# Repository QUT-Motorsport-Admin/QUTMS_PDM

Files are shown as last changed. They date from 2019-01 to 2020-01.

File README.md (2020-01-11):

QUTMS Banner

# Power Distribution Module

Main power distribution for high current devices on the car as well as control of the main LV power busses.

## Features

- ATmega1280 microcontroller
- 4 high and low side outputs
- 9 high current high-side outputs
- 2 Analog inputs
- Onboard thermistor temperature sensor
- CANBUS communication with the MCP2515 controller

## Functions

A key function of the PDM is to power the shutdown loop that runs throughout the car powering the AIRs. This uses one of the high current outputs and the low side of one of the high-low outputs.

The PDM controls power to all of the low voltage devices on the car through a few of its high current outputs. While the current limit on each high current output is 7.5 amps, devices are split onto multiple outputs to allow for future expansion.

Every output on the PDM is controlled using pins on the microcontroller that have PWM capability. This is so devices like pumps and fans can have their speeds modulated. 

The two analog inputs are intended to be used for the radiator temperature sensors since the PDM is also controlling the radiator fans.

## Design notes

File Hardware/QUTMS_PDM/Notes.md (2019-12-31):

# PDM Notes

Outputs with sense wires on the PCB schematic:
- HIC8
- HIC9
- HL3
- HL4

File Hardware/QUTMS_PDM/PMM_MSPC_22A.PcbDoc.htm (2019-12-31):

Reporting Options

# File in Previous Format

Date | : | 19/12/2019
Time | : | 10:54:37 AM
Filename | : | C:\Users\leo2a\Documents\GitHub\QUTMS_PDM\Hardware\QUTMS_PDM\PMM_MSPC_22A.PcbDoc

Version | Warning
Summer 09 | CAUTION - File contains old violation objects. These violations are no longer supported & will not be loaded. Please run DRC after opening this file in order to refresh the violations.
Summer 09 | CAUTION - Existing testpoint rules and settings are used as fabrication testpoint information.
Release 12 | CAUTION - Air Gap Width previously controlled by Clearance rule is now controlled by Polygon Connect Style rule's newly introduced Air Gap Width (set to default value). Suggest reviewing each Polygon Connect Style rule's Air Gap Width attribute for correctness.
Release 13 | CAUTION - Silkscreen Over Component Pads Rules are converted to Silk To Solder Mask Clearance Rules. Suggest examining rule scopes for accuracy.

This file was generated by an earlier version of the software

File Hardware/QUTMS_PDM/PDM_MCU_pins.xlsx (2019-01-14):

Pin | PORT | Function
1 | PORTG 5 | PWM12 | HL3
2 | PORTE 0 | LEDamber
3 | PORTE 1 | LEDgreen
4 | PORTE 2
5 | PORTE 3 | PWM9 | HC9
6 | PORTE 4 | PWM1 | HC3
7 | PORTE 5 | PWM2 | HC2
8 | PORTE 6
9 | PORTE 7
10 | VCC | 5V
11 | GND | GND
12 | PORTH 0
13 | PORTH 1
14 | PORTH 2
15 | PORTH 3 | PWM7 | HC7
16 | PORTH 4 | PWM3 | HC1
17 | PORTH 5 | PWM4 | HC4
18 | PORTH 6 | PWM11 | HL2
19 | PORTB 0 | SS
20 | PORTB 1 | SCK
21 | PORTB 2 | MOSI
22 | PORTB 3 | MISO
23 | PORTB 4 | PWM10 | HL1
24 | PORTB 5
25 | PORTB 6
26 | PORTB 7 | PWM13 | HL4
27 | PORTH 7
28 | PORTG 3
29 | PORTG 4
30 | RESET | RST
31 | VCC | 5V
32 | GND | GND
33 | XTAL2 | XT
34 | XTAL1 | XT
35 | PORTL 0
36 | PORTL 1 | PWM5 | HC5
37 | PORTL 2 | PWM8 | HC8
38 | PORTL 3 | PWM6 | HC6
39 | PORTL 4
40 | PORTL 5
41 | PORTL 6
42 | PORTL 7
43 | PORTD 0
44 | PORTD 1
45 | PORTD 2
46 | PORTD 3
47 | PORTD 4
48 | PORTD 5
49 | PORTD 6
50 | PORTD 7
51 | PORTG 0 | HL34_DISABLE
52 | PORTG 1 | HL34_ENABLE
53 | PORTC 0
54 | PORTC 1
55 | PORTC 2
56 | PORTC 3
57 | PORTC 4
58 | PORTC 5
59 | PORTC 6
60 | PORTC 7
61 | VCC | 5V
62 | GND | GND
63 | PORTJ 0
64 | PORTJ 1 | HL34_status
65 | PORTJ 2 | HL12_status
66 | PORTJ 3 | HL12_enable
67 | PORTJ 4 | HL12_disable
68 | PORTJ 5 | CAN_RX0_buf
69 | PORTJ 6 | CAN_INT
70 | PORTG 2 | HIC9_ser
71 | PORTA 7 | HL4_ser
72 | PORTA 6 | HIC8_ser
73 | PORTA 5 | HL3_ser
74 | PORTA 4 | AN2_bias
75 | PORTA 3 | AN1_bias
76 | PORTA 2 | CAN_TX0_RTS
77 | PORTA 1 | CAN_RST
78 | PORTA 0 | CAN_select
79 | PORTJ 7
80 | VCC | 5V
81 | GND | GND
82 | PORTK 7 | Vbatt
83 | PORTK 6 | 5V
84 | PORTK 5 | AN2
85 | PORTK 4 | AN1
86 | PORTK 3 | Thermistor
87 | PORTK 2 | HC5_current
88 | PORTK 1 | HC4_current
89 | PORTK 0 | HC3_current
90 | PORTF 7 | HC2_current
91 | PORTF 6 | HL34_current
92 | PORTF 5 | HL12_current
93 | PORTF 4 | HC9_current
94 | PORTF 3 | HC8_current
95 | PORTF 2 | HC6_current
96 | PORTF 1 | HC7_current
97 | PORTF 0 | HC1_current
98 | AREF | AREF
99 | GND | GND
100 | AVCC | AVCC

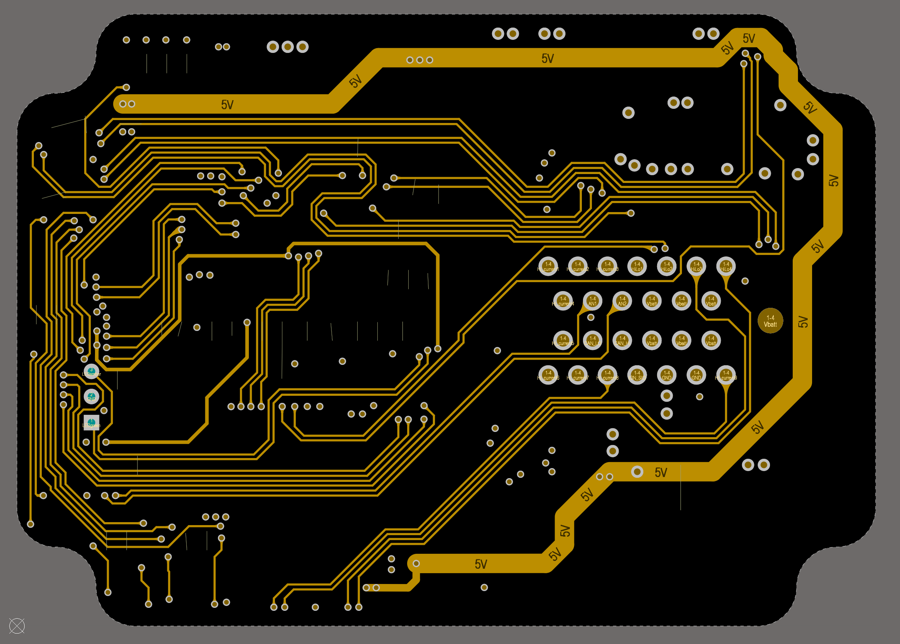
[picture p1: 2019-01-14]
Hardware/QUTMS_PDM/PDMMid.PNG

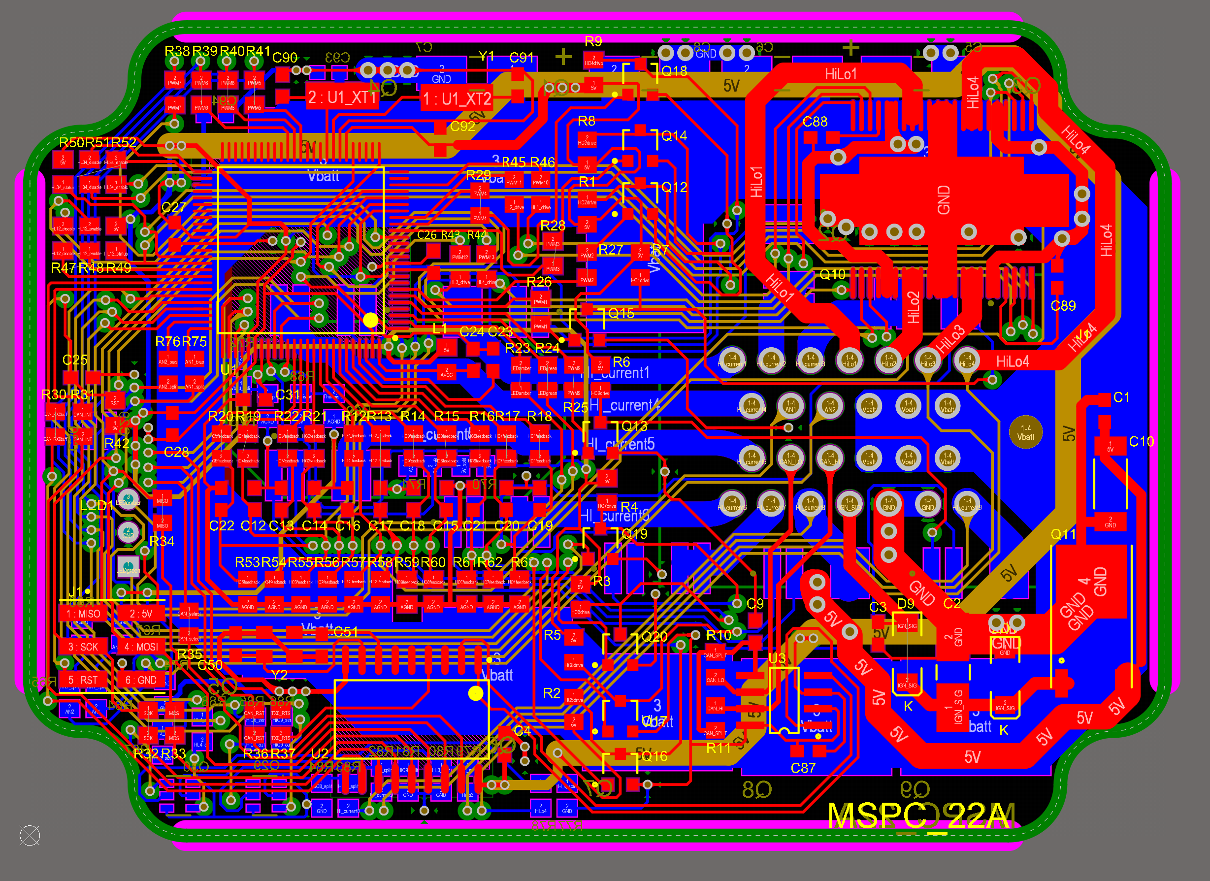
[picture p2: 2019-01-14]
Hardware/QUTMS_PDM/PDMAll.PNG

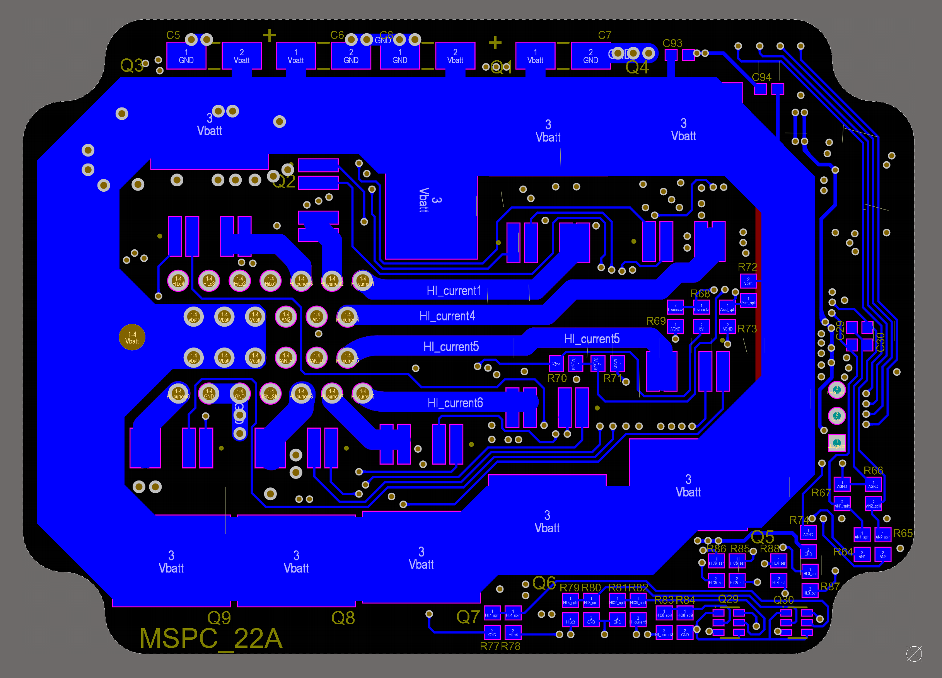
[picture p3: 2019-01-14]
Hardware/QUTMS_PDM/PDMBtmFlipped.PNG

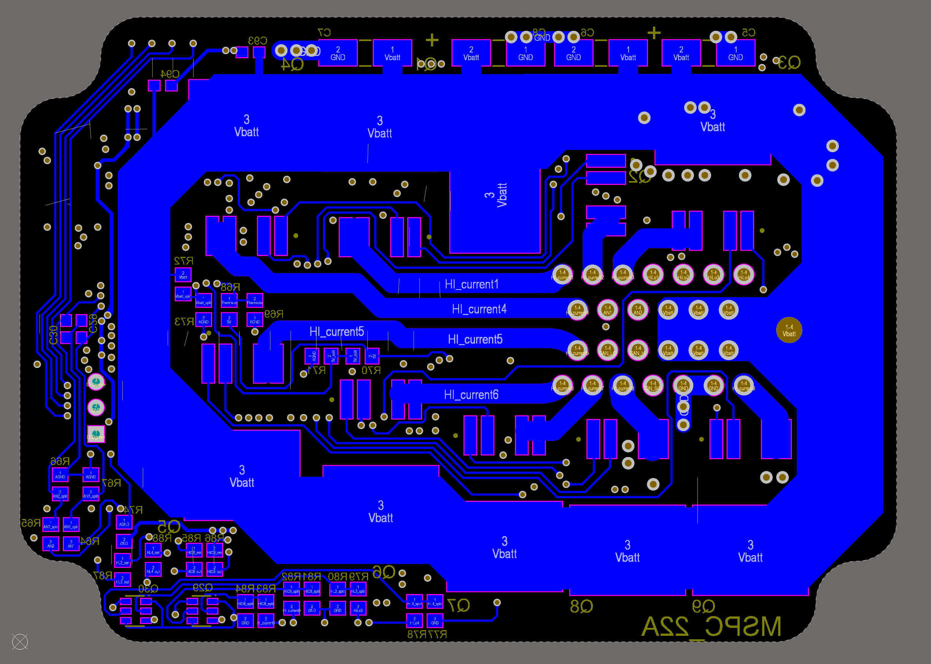
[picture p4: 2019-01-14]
Hardware/QUTMS_PDM/PDMBtm.PNG

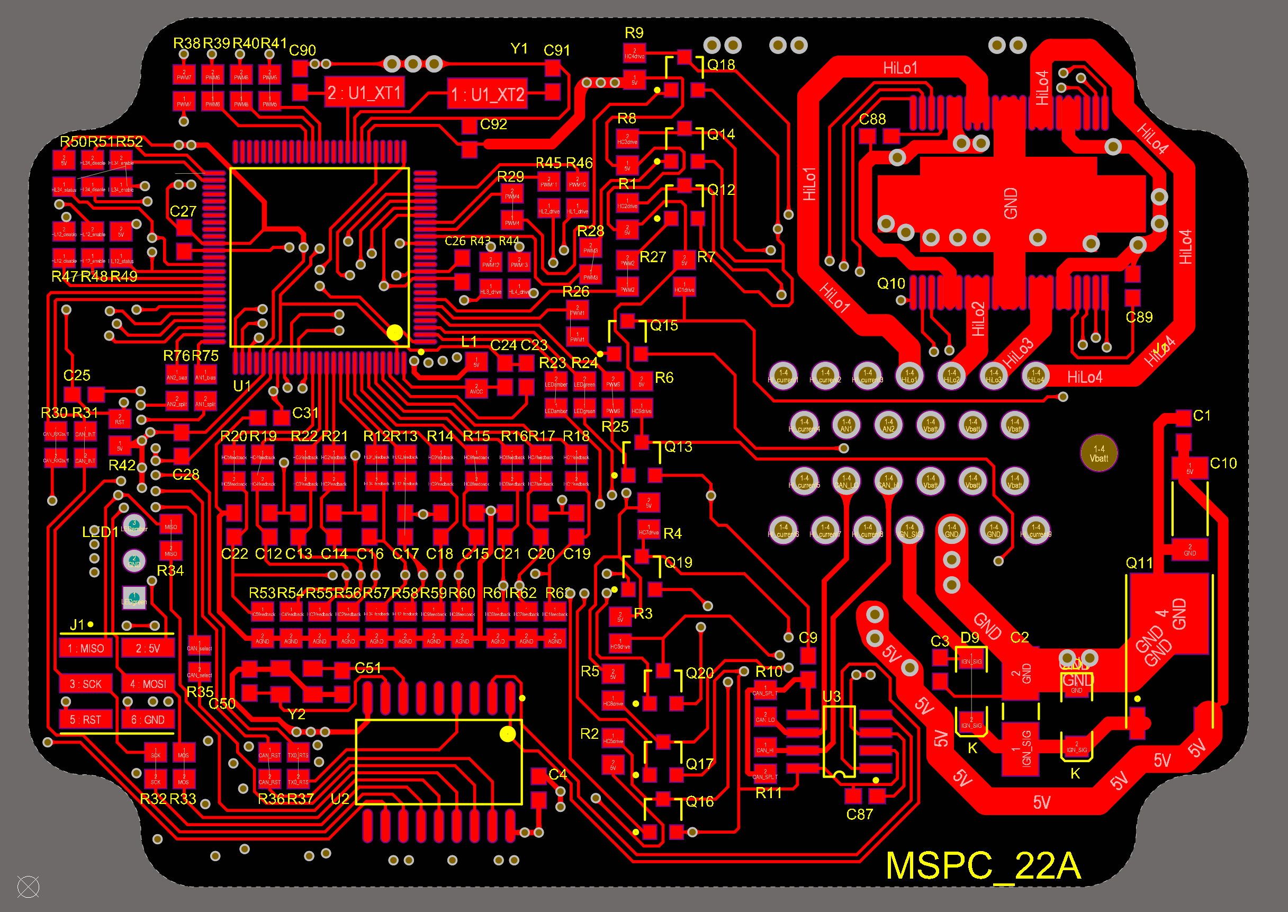
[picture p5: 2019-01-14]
Hardware/QUTMS_PDM/PDMTop.PNG

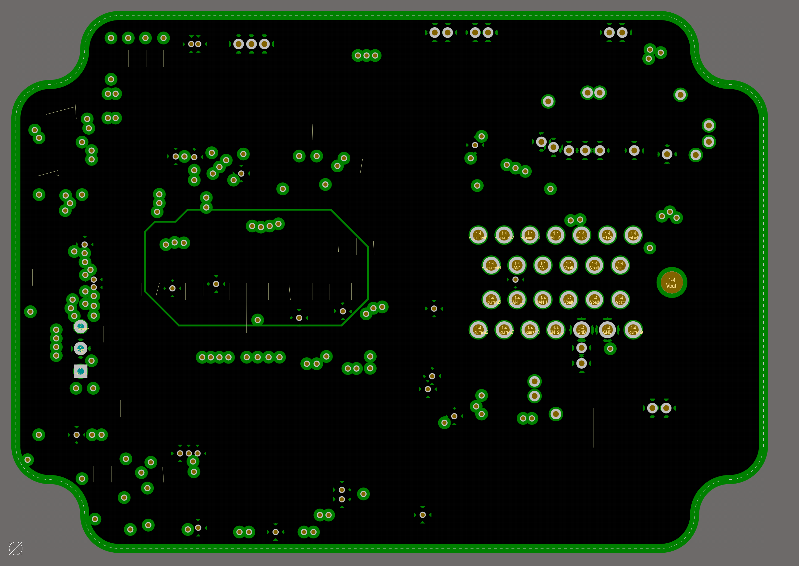
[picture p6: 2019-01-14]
Hardware/QUTMS_PDM/PDMGnd.PNG

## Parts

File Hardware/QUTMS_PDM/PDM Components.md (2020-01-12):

PDM Components

ID		NAME		QTY		DESC
---		---			---		---
C1		?			1		106 50K (144/Q51)
C2-8	2521 Cap	1		106 50K (144/Q51)
C10		2521 Cap	1		106 50K (144/Q51)
C90		0603 Cap	1		22pf 16V Ceramic
C91		0603 Cap	1		22pf 16V Ceramic
Y1		A16012X		1		16Mhz Crystal
U1		ATMEGA1280	1		Microcontroller
U2		MCP2515		1		CAN Controller
U3		
Q1-Q9	AUIR3320S	9		Alternative: AUIR3313STRL
Q10 	MC33932VW	1
Q12-Q20	1702A		9
Q29-Q30 X17			2		
J1		2x3 Header	1		ICSP Programming Header
L1		0805		1		Inductor
R1-11	0603 ?Ω		10		Unpopulated Resistor
R12-22	0603 10kΩ	10		Resistor
R30-37	0603 0Ω		8		Resistor
R38-41	0603 1kΩ	4		Resistor

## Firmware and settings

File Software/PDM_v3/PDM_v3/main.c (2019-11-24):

/*
 * PDM_v3.c
 *
 * Updated : 6/03/2019 4:09:20 PM	
 * Created : 8/22/2018 9:05:36 AM
 * Authors : Zoe Goodward, Anthony Kellam
 */ 

#define F_CPU 16000000UL
#include <avr/io.h>
#include <util/delay.h>
#include <avr/interrupt.h>
#include "main.h"
#include "SPI.h"
#include "pdmCAN.h"
#include "MCP2515.h"

#define CAN_ID_PDM 0x09000001 /* CAN Bus Identifier for PDM */
#define CHECK_BIT(var,pos) ((var) & (1<<(pos)))

int main(void) {	
    firmware_init();
    sei();

	//Permanently energised boards
	board_init();
	
    while(1) {
		/* Wait for CAN interrupts */	
		CAN_read_packet();
		_delay_ms(100);
		amberOFF;
		greenOFF;
		_delay_ms(100);
	}
}

void firmware_init(void) {
	io_init();
    PCICR |= (1<<PCIE1); // Turning on PCIE1 bit in PCICR register
    PCMSK1 |= (1<<PCINT15); // Turning on the PCINT15 bit in PCMSK1 register
    SPI_init();
    MCP2515_init(POWER_CAN);
}

void board_init(void) {
	//Permanently energised boards
	HL12enableON;	// D1 of MC33932 - Disable state on: OUT1 & OUT2 are 3-state disabled  -  D1 input is used to 3-state disable the H-bridge outputs.
	HL34enableON;	//
	
	HC1ON;			//chassis controller power on
	HC2ON;			//BMS power on
	HC3ON;			//shutdown positive on - will be changed
	HLchan2OFF;		//shutdown negative on - will be changed
	HLchan4ON;		//inverter power on
	HC8ON;			//steering wheel and radio power on
}

/**
 * @brief Configures the pins required for IO. Each port pin consists of three register bits: DDxn, PORTxn, and PINxn set by the following registers
 * 
 * 	DDRx   - Sets the direction of PINxn in bit DDxn (1 -> output, 0 -> input)
 * 
 * 	PORTx  - Activates the pull-up resistor for PINxn in bit PORTxn. The pull-up resistor will only be activated if written as logic 1 AND set as an input
 * 
 *  PINx   - The Port Input Pins I/O location is read only. 
 *           Writing a logic one to a bit in the PINx Register, will result in a toggle in the corresponding bit in the Data Register.
 * 		     Writing a logic one to PINxn toggles the value of PORTxn, independent on the value of DDRxn
 * 
 * Reference: ATmega Datasheet Chapter 13 (I/O-Ports)
 * 
 */
void io_init(void) {
	DDRA |= 0b00000001;		//PA0 - CAN_SS // chip select
	DDRB |= 0b10010110;		//PB7 PWM13; PB4 PWM10; PB2 MOSI; PB1 SCK
	DDRD |= 0b00000000;		//nil
	DDRE |= 0b00111011;		//PE5 PWM2; PE4 PWM1; PE3 PWM9; PE1 greenLED; PE0 amberLED
	DDRG |= 0b00100011;		//PG5 PWM12; PG1 HL34enable; PG0 HL34disable
	DDRH |= 0b01111000;		//PH6 PWM11; PH5 PWM4; PH3 PWM3; PH2 PWM7
	DDRJ |= 0b00011000;		//PJ4 HL12disable; PJ3 HL12enable
	DDRL |= 0b00111000;		//PL3 PWM6; PL2 PWM8; PL1 PWM5
	
	PORTA &= ~0b00000001;	//CAN_SS off
	PORTB &= ~0b10010110;	//PWMs off; MOSI off
	PORTD &= ~0b11000000;	//HL34enable off; HL34disable on
	PORTE &= ~0b00111110;	//3 x PWMs off; LEDs off
	PORTG &= ~0b00100011;	//PWM12 off
	PORTH &= ~0b01111000;	//4 x PWMs off; HL34disable on; HL34enable off
	PORTJ &= ~0b00011000;	//HL12disable on; HL12enable off
	PORTL &= ~0b00111000;	//3 x PWMs off
}

void CAN_read_packet() {
	uint8_t data[8];
	uint32_t ID;
	uint8_t numBytes;
	amberON;
	CAN_pull_packet(POWER_CAN, &numBytes, data, &ID);
	if (ID == CAN_ID_PDM) {
		if(numBytes > 3) {
			greenON;
			} else {
			greenOFF;
		}
		/* Byte 1 */
		if (CHECK_BIT(data[0], 0)) { /* Pump RHS */
			HC4ON;
			} else {
			HC4OFF;
		}
		if (CHECK_BIT(data[0], 1)) { /* Fan RHS */
			HC5ON;
			} else {
			HC5OFF;
		}
		if (CHECK_BIT(data[0], 2)) { /* Pump LHS */
			HC6ON;
			} else {
			HC6OFF;
		}
		if (CHECK_BIT(data[0], 3)) { /* Fan LHS */
			HC7ON;
			} else {
			HC7OFF;
		}
		if (CHECK_BIT(data[0], 4)) { /* Brake */
			HLchan1ON;
			} else {
			HLchan1OFF;
		}
		if (CHECK_BIT(data[0], 5)) {  /* Siren */
			HC9ON;
			} else {
			HC9OFF;
		}
		if (CHECK_BIT(data[0], 6)) { /* Shutdown - On */
			HLchan2ON;
			} else {
			HLchan2OFF; // Test?
		}
		if (CHECK_BIT(data[0], 7)) { /* Shutdown + On */
			HC3ON;
			} else {
			HC3OFF;
		}
		/* Byte 2 */

		/* Byte 3 */

		/* Byte 4 */

		/* Byte 5 */
	}
}

/**
 * @brief Called whenever CANBUS interrupt is triggered
 * CAN Packet 1
 * Byte 1													| Byte 2			| Byte 3			| Byte 4			| Byte 5			|
 * 0b  0,     0,     0,     0,     0,      0,     0,      0	| 0b00000000		| 0b00000000		| 0b00000000		| 0b00000000		|
 * SHDN+, SHDN-, Siren, Brake, Fan L, Pump L, Fan R, Pump R	| Fan L PWM 0-100	| Pump L PWM 0-100 	| Fan R PWM 0-100	| Pump R PWM 0-100	|
**/
ISR(PCINT1_vect) {	
	uint8_t data[8];
	uint32_t ID;
	uint8_t numBytes;
	amberON;
	CAN_pull_packet(POWER_CAN, &numBytes, data, &ID);
	if (ID == CAN_ID_PDM) {
		if(numBytes > 3) {	
			greenON;
		} else {
			greenOFF;
		}
		/* Byte 1 */
		if (CHECK_BIT(data[0], 0)) { /* Pump RHS */
			HC4ON;
		} else {
			HC4OFF;
		} 
		if (CHECK_BIT(data[0], 1)) { /* Fan RHS */
			HC5ON;
		} else {
			HC5OFF;
		}
		if (CHECK_BIT(data[0], 2)) { /* Pump LHS */
			HC6ON;
		} else {
			HC6OFF;
		}
		if (CHECK_BIT(data[0], 3)) { /* Fan LHS */
			HC7ON;
		} else {
			HC7OFF;
		}
		if (CHECK_BIT(data[0], 4)) { /* Brake */
			HLchan1ON;
		} else {
			HLchan1OFF;
		}
		if (CHECK_BIT(data[0], 5)) {  /* Siren */
			HC9ON;
		} else {
			HC9OFF;
		}
		if (CHECK_BIT(data[0], 6)) { /* Shutdown - On */
			HLchan2ON;
		} else {
			HLchan2OFF; // Test?
		}
		if (CHECK_BIT(data[0], 7)) { /* Shutdown + On */
			HC3ON;
		} else {
			HC3OFF;
		}
		/* Byte 2 */

		/* Byte 3 */

		/* Byte 4 */

		/* Byte 5 */
	}
}

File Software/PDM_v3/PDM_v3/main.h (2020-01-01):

/*
 * main.h
 *
 * Created: 8/22/2018 9:46:53 AM
 *  Author: Ant
 */ 


#ifndef MAIN_H_
#define MAIN_H_

/* LEDS */
#define greenON PORTE |= 2
#define amberON PORTE |= 1
#define greenOFF PORTE &= ~2
#define amberOFF PORTE &= ~1
#define greenTOGGLE PORTE ^= ~2
#define amberTOGGLE PORTE ^= ~1


#define HL12enableON PORTJ |= 8
#define HL12enableOFF PORTJ &= ~8

#define HL34enableON PORTG |= 2
#define HL34enableOFF PORTG &= ~2

/* Brake Light */
#define HLchan1ON PORTB |= 16		// Brake Light On
#define HLchan1OFF PORTB &= ~16		// Brake Light Off

/* Shutdown - */
#define HLchan2ON PORTH |= 64
#define HLchan2OFF PORTH &= ~64		// Shutdown - On (0b01000000)

#define HLchan3ON PORTG |= 32
#define HLchan3OFF PORTG &= ~32

/* Invertors */
#define HLchan4ON PORTB |= 128		// Inverter Power On
#define HLchan4OFF PORTB &= ~128	// Inverter Power Off

/* Chassis Controller */
#define HC1ON PORTH |= 16;		// Chassis Controller On 
#define HC1OFF PORTH &= ~16;	// Chassis Controller Off

/* BMS */	
#define HC2ON PORTE |= 32;		// BMS On
#define HC2OFF PORTE &= ~32;	// BMS Off

/* Shutdown + */	
#define HC3ON PORTE |= 16;		// Shutdown + On
#define HC3OFF PORTE &= ~16;	// Shutdown + Off

/* Pump RHS */
#define HC4ON PORTH |= 32;		// Pump RHS On
#define HC4OFF PORTH &= ~32;	// Pump RHS Off

/* Fan RHS */
#define HC5ON PORTL |= 8;		// Fan RHS On
#define HC5OFF PORTL &= ~8;		// Fan RHS On

/* Pump LHS */
#define HC6ON PORTL |= 32;		// Pump LHS On
#define HC6OFF PORTL &= ~32;	// Pump LHS Off

/* Fan LHS */
#define HC7ON PORTH |= 8;		// Fan LHS On
#define HC7OFF PORTH &= ~8;		// Fan LHS Off

/* Radio, Dash, Steering Wheel */
#define HC8ON PORTL |= 16;		// Radio, Dash, Steering Wheel On
#define HC8OFF PORTL &= ~16;	// Radio, Dash, Steering Wheel Off

/* RTD Siren */
#define HC9ON PORTE |= 8;		// RTD On
#define HC9OFF PORTE &= ~8;		// RTD Off

/* Functions */
void io_init();
void firmware_init();
void external_interrupt_init();
void board_init();
void pwm_init();
void CAN_read_packet();

#endif /* MAIN_H_ */

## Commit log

2019-01-14 Initial commit, all associated PDM files uploaded
    [PDMTest.SchDoc, PDM_MCU_pins.xlsx, PMM_MSPC_22A.PcbDoc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]
2019-02-08 Add V3 of software, no CAN functionality
    [PDMTest.SchDoc, PDM_MCU_pins.xlsx, PMM_MSPC_22A.PcbDoc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]
2019-02-20 (Zoe) Changed startup sequence, started adding in CANBUS functionality
2019-03-06 Add functionality to read CAN message and turn on and off peripheral devices
2019-11-24 Poll CAN packets instead of waiting for interrupt (as it is not currently triggering)
2019-12-31 Partial reverse engineering of the PCB. Still needs output MOSFETs and other bits and bobs.
    [CANBUS.SchDoc, MCU.SchDoc, Outputs.SchDoc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]
2020-01-03 current working fuse configuration
2020-01-12 add alternative mosfet
2020-01-18 Added schematic for main mosfets
    [AUIR3313STRL.SchLib]
2020-01-18 made some changes. linked some components
    [CANBUS.SchDoc, MCU.SchDoc, Outputs.SchDoc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]
2020-01-18 Add 26 pos superseal connector
    [6473418-1.PcbLib, 6473418-1.SchLib, ExternalConnections.SchDoc]
